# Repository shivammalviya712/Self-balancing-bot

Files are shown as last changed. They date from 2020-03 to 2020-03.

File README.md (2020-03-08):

# Objective

The objective is to make a remote control robot capable of balancing itself using Linear Quadratic Regulator (LQR) Control.

# Components
- Arduino Mega
- MPU 6050 (Accelerometer + Gyroscope)
- DC Motors with quadrature encoders
- Xbee Module 
- Motor Driver (L298N)
- 12V Lipo Battery
- Chassis
- Breadboard
- Wheels

# 3D Model of Chassis
- 3D Modelling of the robot is done in the solidworks, and those files are available in 3D Model folder.
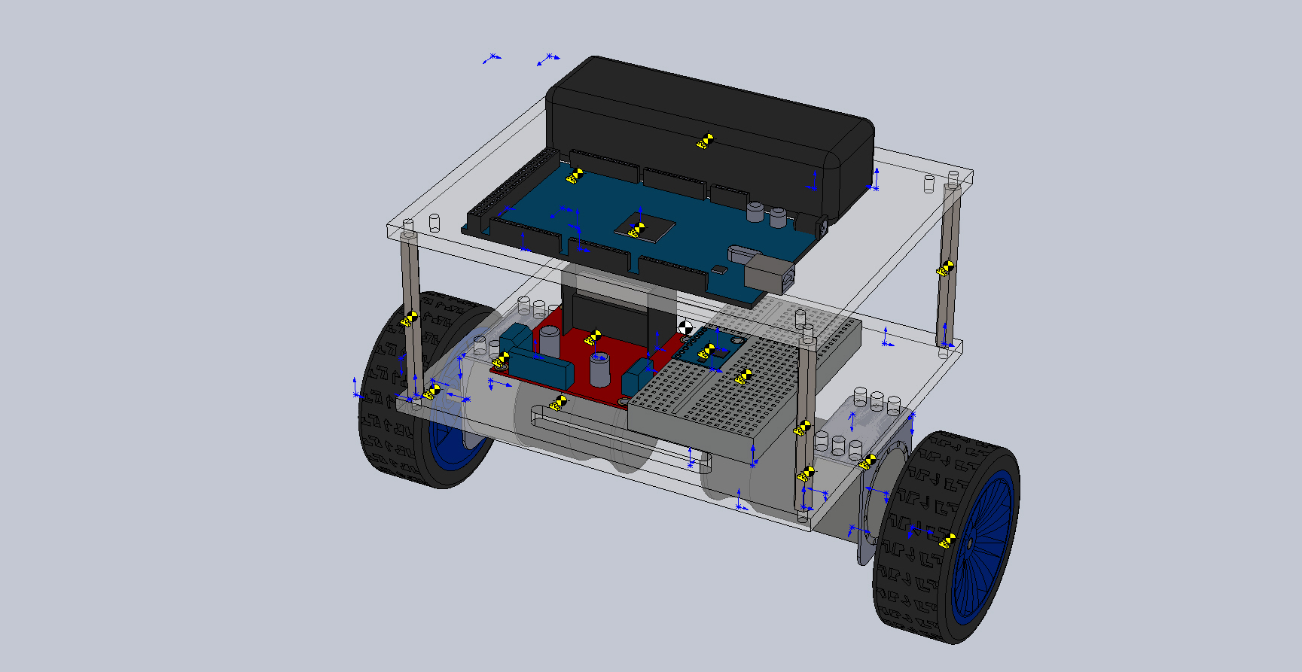
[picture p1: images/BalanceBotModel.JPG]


# Mathematical Model
- Derivations are given in the folder Mathematical Model.
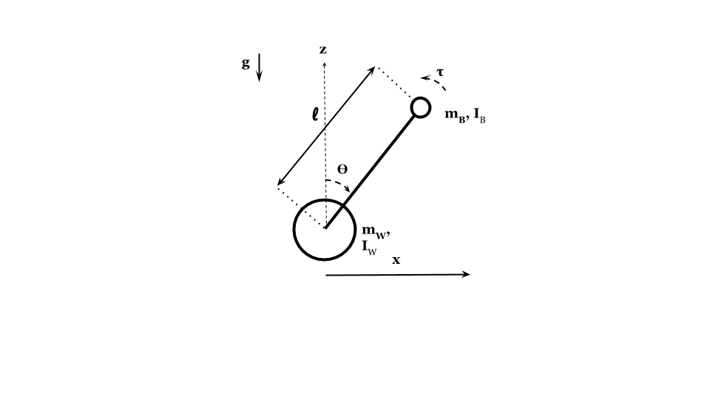
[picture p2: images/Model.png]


- State-Space Equation
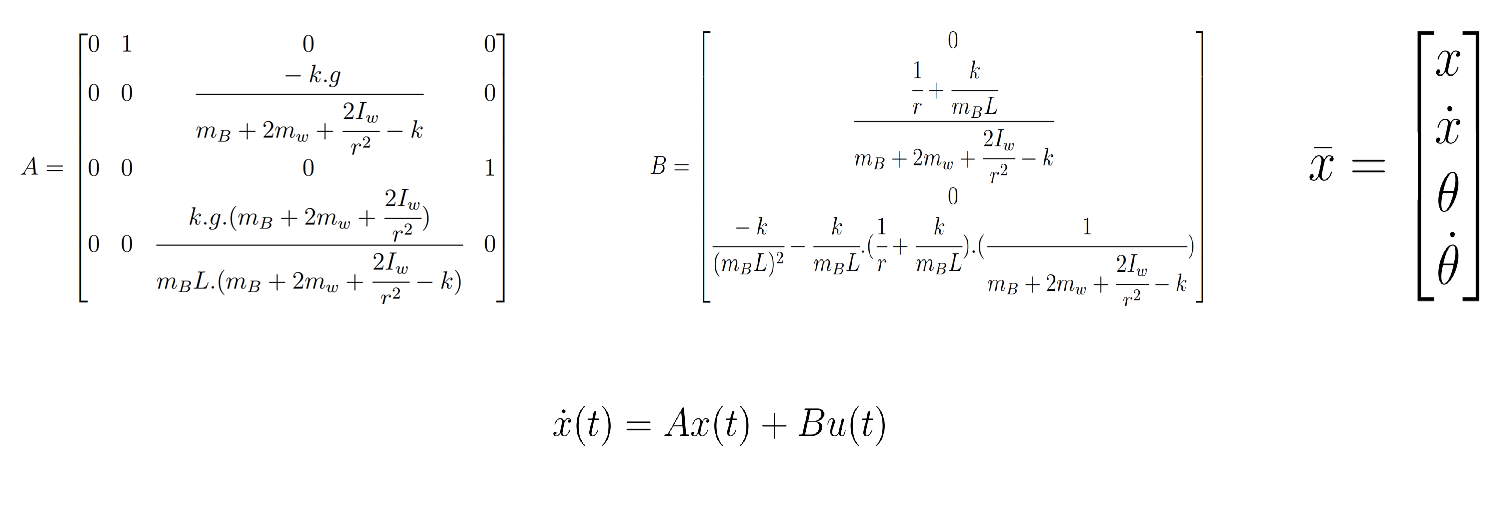
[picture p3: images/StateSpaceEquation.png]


# Control Architecture
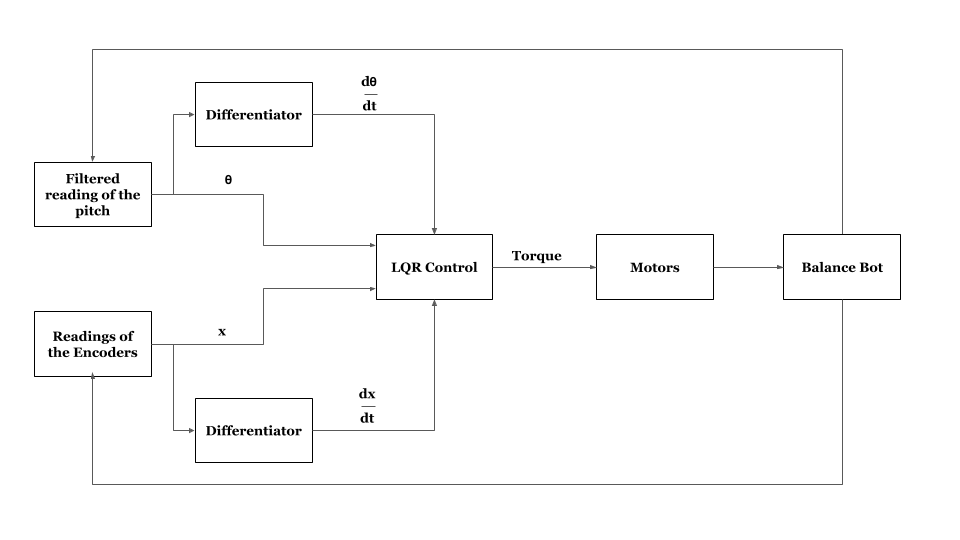
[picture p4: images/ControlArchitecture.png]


- Filter
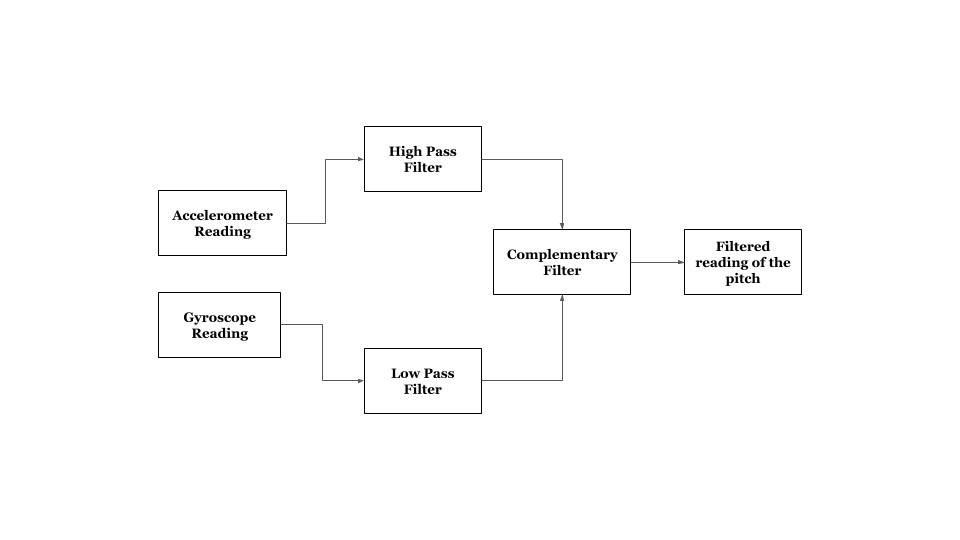
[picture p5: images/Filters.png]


# Code Structure

## main.ino
- This is the file in which code for controlling Arduino Mega is written.

## Encoders
- In these files, class of encoders is defined.  
- X4 encoding is used.

## Motor
- In these files, class of motor is defined.
- Encoder is a inner class of motor.

## TimerInterruptsLib
- Timers 3, 4, and 5 are initialized in this library.

## RCModule
- In this files, class of Xbee is defined.

## Octave
- In this files, dicrete state-space model of robot is calculated from its continuous state-space model.
- State variables are simulated from given Q and R matrix.

# Requirements
- Arduino IDE
  - digitalWriteFast.h
  - MPU6050
  - MPULib
  - I2C
  - I2Cdev
  
- Octave
  - "control" package

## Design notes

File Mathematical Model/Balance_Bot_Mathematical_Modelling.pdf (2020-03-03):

# Mathematical Modelling

mB = Mass of the body
mw = Mass of the wheel
IB = Moment of inertia of the body about the axis of wheels
Iw = Moment of inertia of the wheel
L = Height of the centre of mass of the body from the centre of the wheels r = Radius of the wheels
T = Torque due to both the wheels

φ = The angular velocity of the wheel about its axis of rotation. x = Position of centre of mass of wheel along x-axis
x˙ = Linear velocity of centre of mass of the wheel
θ = Angle between z-axis and body of the robot
˙θ = Angular velocity of the body

Ek = Kinetic Energy
Ep = Potential Energy with the plane through centre of mass of wheels as reference

Assuming the motion of wheels to be pure rolling
x = rφ

φ˙ =

x˙
r

Derivation

Ek = (mw +

mB
2

+

Iw
r

2

)( ˙x)

2 +

(mBL

2 + IB)

2

(

˙θ)

2 + mBL ˙θx˙ cos(θ)

Ep = mBgL cos(θ)

L = Ek − Ep = (mw +

mB
2

+

Iw
r

2

)( ˙x)

2 +

(mBL

2 + IB)

2

(

˙θ)

2 + mBL ˙θx˙ cos(θ) − mBgL cos(θ)

∂L
∂θ = mBL sin(θ)(g − ˙θx˙)

d
dt(

∂L
∂

˙θ

) = (mBL

2 + IB)

¨θ + mBLx¨ cos(θ) − mBLx˙

˙θ sin(θ)

∂L
∂x = 0

d
dt(

∂L
∂

˙θ

) = (mB + 2mw + 2

Iw
r

2

)¨x + mBL¨θ cos(θ) − mBL ˙θ
2
sin(θ)

1

By Euler-Lagrange Equation Q = Generalised Force
q = Generalised Co-ordinates d
dt(

∂L
∂q˙

) −

∂L
∂q = Q

Equations of Motion

¨θ =

mBgL sin(θ) − mBLx¨ cos(θ) − T (mBL² + IB)

(mB + 2mw + 2

Iw
r

2

)¨x + mBL¨θ cos(θ) − mBL ˙θ
2
sin(θ) =

T
r

For sake of simplicity let’s take k =

m²
BL

2
mBL² + IB
From Equations of Motion

x¨ =

1

mB + 2mw +

2Iw
r

2

− kcos(θ)

2

.(−k.g.cos(θ).sin(θ) + mBL

2 ˙θ
2
sin(θ) + (

1
r

+

k.cos(θ)
mBL

).T)

x¯ =

x
x˙
θ
˙θ

By solving x¯˙ = f(¯x) = 0 the equilibrium point we get are :

x
0
0
0

(Unstable),

x
0
π
0

(Stable)

Here x (first element of x¯) is free to take any value.

Let’s x¯o =

x
0
0
0

(Unstable Equilibrium)

Linearising x¯˙ = f(¯x) about x¯o ∂x¨
∂x(at x¯o) = 0

∂x¨
∂x˙

(at x¯o) =

1

mB + 2mw +

2Iw
r

2

− k

.0 = 0

2

∂
x¨
∂θ

(at

x¯o) =

1

m

B + 2

m
w

+

2

### Iwr²

−

k.(

−k.g

)

∂
x¨
∂ ˙θ

(at

x¯o) =

1

m

B + 2

m
w

+

2

### Iwr²

−

k.0 = 0

∂
x¨
∂T

(at

x¯o) =

1r
+

k
m
B

L

m

B + 2

m
w

+

2

### Iwr²

−
k

¨θ
=

k.g.sin

(
θ

)
m
B

L

−

k.x.cos ¨

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
x¯o) = 0

∂

¨θ

∂

x˙(at

x¯o) = 0

∂

¨θ

∂θ

(at

x¯o) =

k.g mBL. m

B + 2

m
w

+

2

### Iwr²

m

B + 2

m
w

+

2

### Iwr²

−
k

∂

¨θ

∂ ˙θ

(at

x¯o) = 0

∂

¨θ

∂T

(at

x¯o) =

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
). | 1 mB + 2mw

+

2

### Iwr²

−
k

A
=
0 1 | 0 | 0
0 0 | − k.g

m

B + 2

m
| w

+

2

### Iwr²

−
k
| | 0
0 0 | 0 | 1

0 0

k.g.

(
m
| B + 2

m
w

+

2

### Iwr²

)

m

BL.

(
m
| B + 2 m
w

+

2

### Iwr²

−
k

)

| | 0

3

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

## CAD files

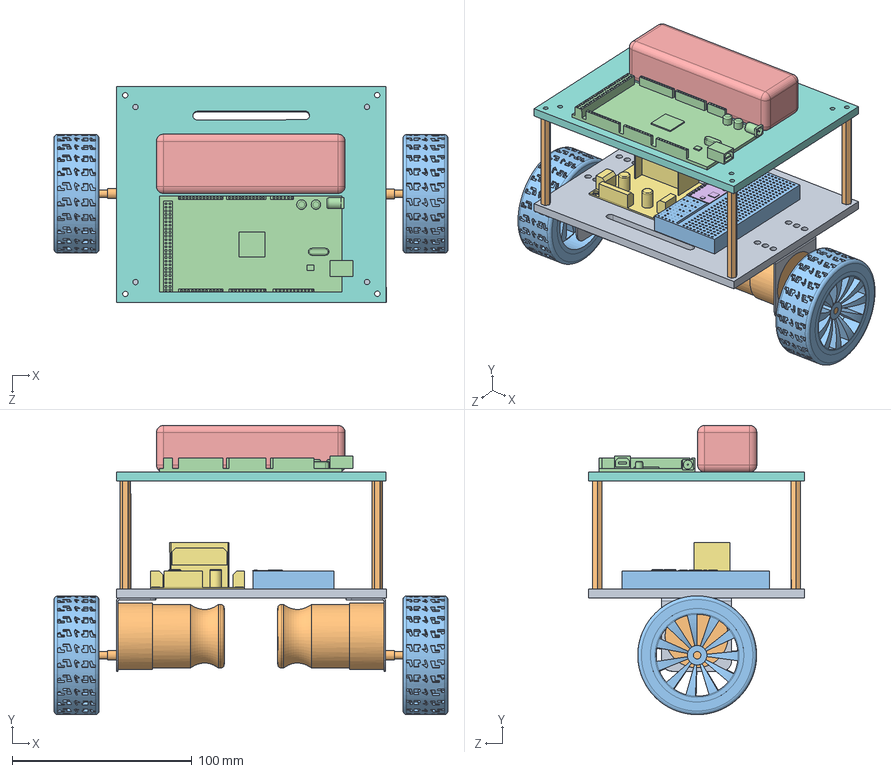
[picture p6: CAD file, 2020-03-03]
3D Model/Balance Bot/Bot.SLDASM
219.1 x 160.8 x 120.1 mm
Motor clamp x 2
Motor x 2
Wheel x 2
Arduino Mega
Battery
GY87
Motor driver
MidPlate
BottomPlate
Rod(6) x 4
Breadboard

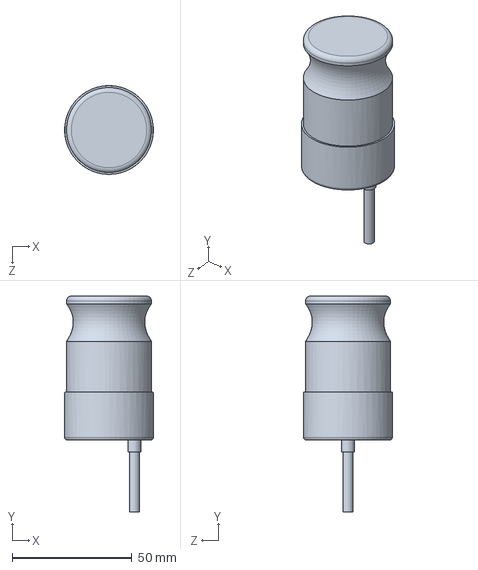
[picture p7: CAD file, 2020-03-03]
3D Model/Balance Bot/Motor.SLDPRT
37.0 x 90.0 x 37.0 mm

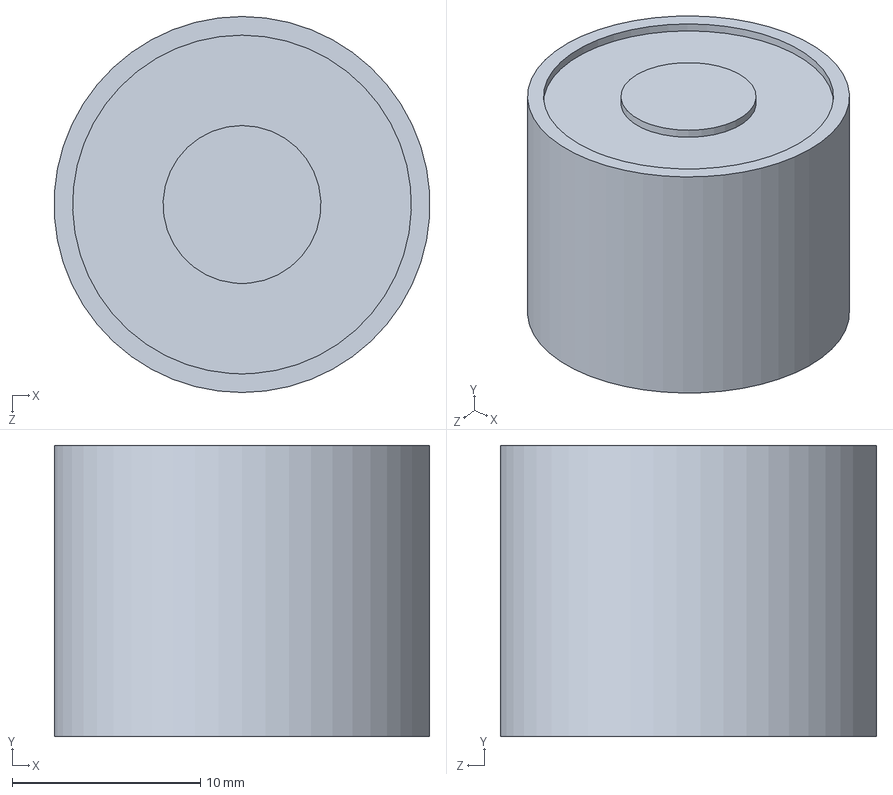
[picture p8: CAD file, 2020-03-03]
3D Model/Balance Bot/Electromagnet.SLDPRT
20.0 x 15.5 x 20.0 mm

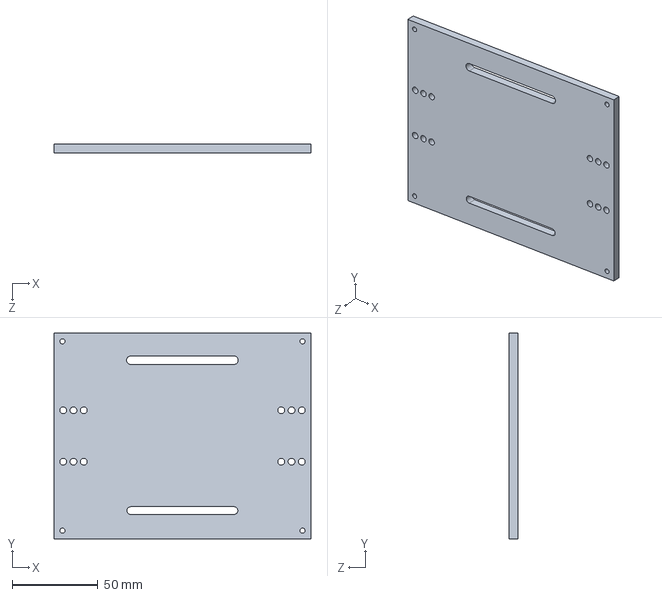
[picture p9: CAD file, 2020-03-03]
3D Model/Balance Bot/BottomPlate.SLDPRT
150.0 x 120.0 x 5.00 mm

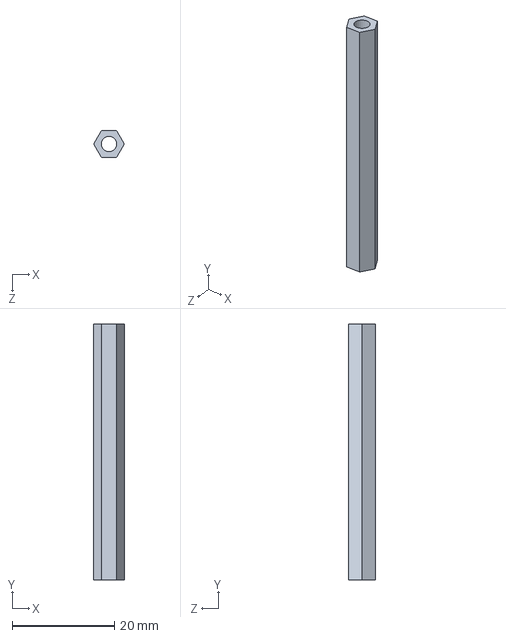
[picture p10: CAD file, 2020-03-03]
3D Model/Balance Bot/Rod(5).SLDPRT
6.00 x 50.0 x 5.20 mm

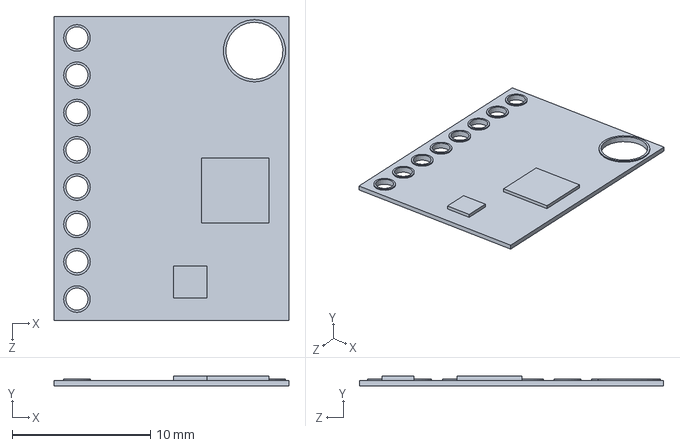
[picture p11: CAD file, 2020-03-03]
3D Model/Balance Bot/GY87.SLDPRT
17.0 x 0.7 x 22.0 mm

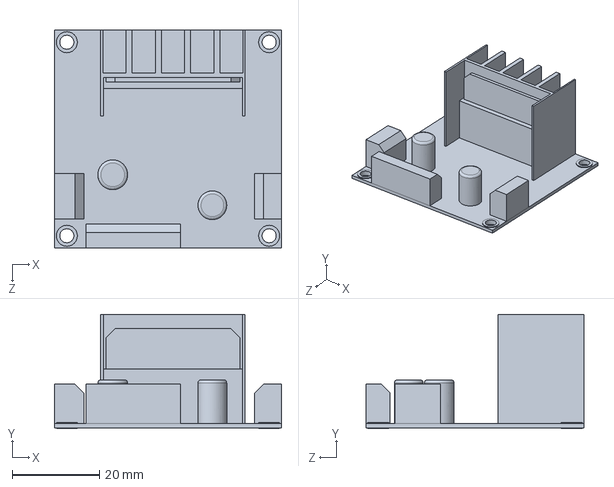
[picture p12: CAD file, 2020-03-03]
3D Model/Balance Bot/Motor driver.SLDPRT
52.0 x 26.2 x 50.0 mm

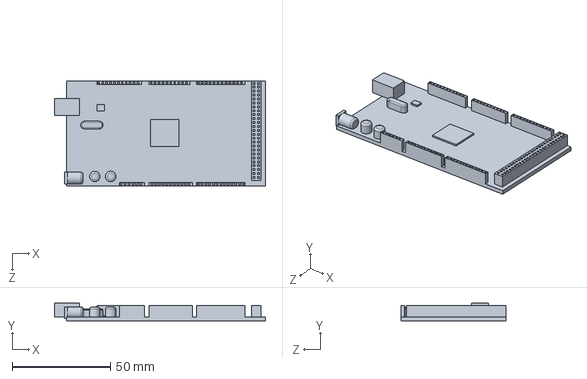
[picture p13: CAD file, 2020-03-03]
3D Model/Balance Bot/Arduino Mega.SLDPRT
107.5 x 9.00 x 53.3 mm

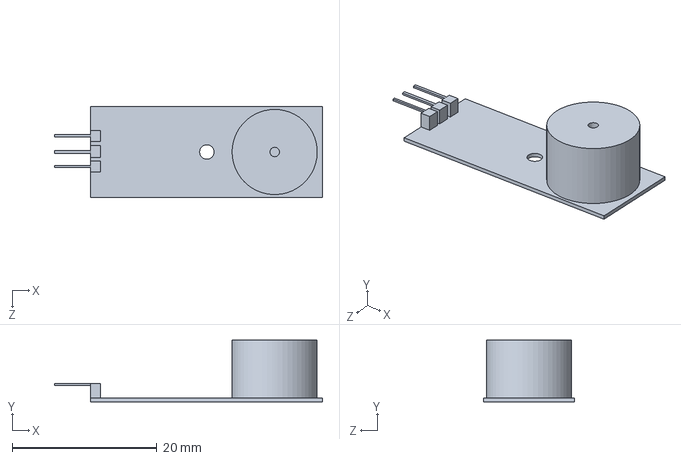
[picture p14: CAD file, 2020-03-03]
3D Model/Balance Bot/Buzzer.SLDPRT
37.0 x 8.50 x 12.5 mm

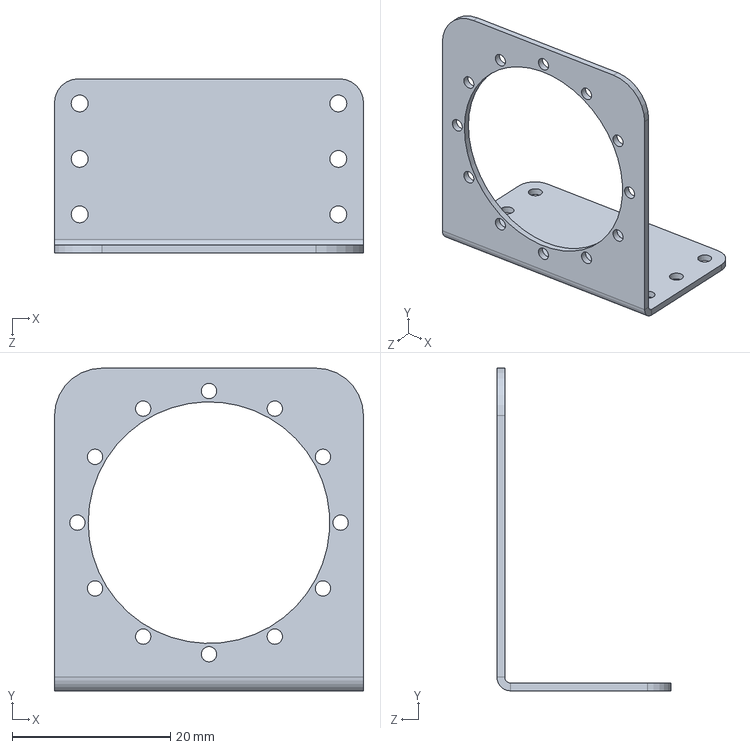
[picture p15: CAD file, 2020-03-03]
3D Model/Balance Bot/Motor clamp.SLDPRT
39.0 x 40.7 x 22.0 mm

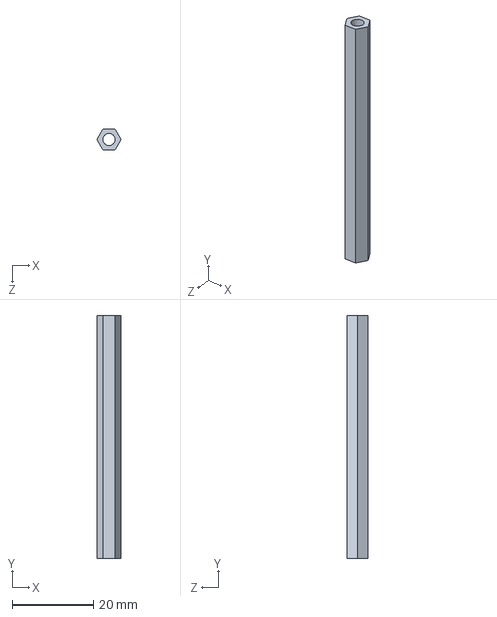
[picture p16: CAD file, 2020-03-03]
3D Model/Balance Bot/Rod(6).SLDPRT
6.00 x 60.0 x 5.20 mm

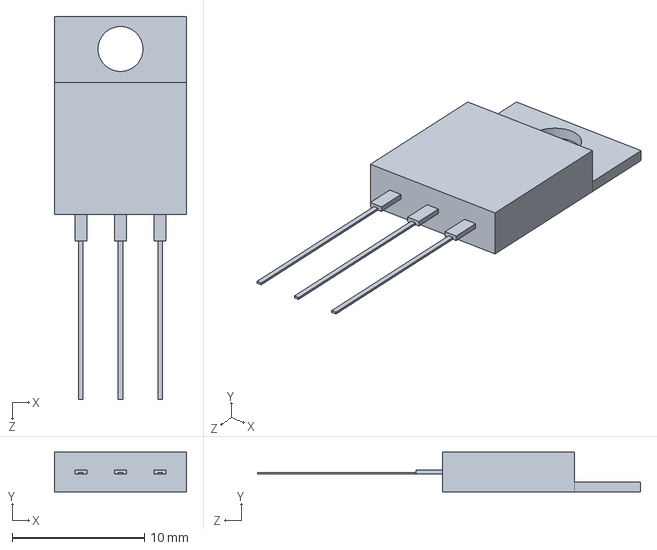
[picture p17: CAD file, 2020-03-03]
3D Model/Balance Bot/IRF540N.SLDPRT
10.0 x 3.00 x 29.0 mm

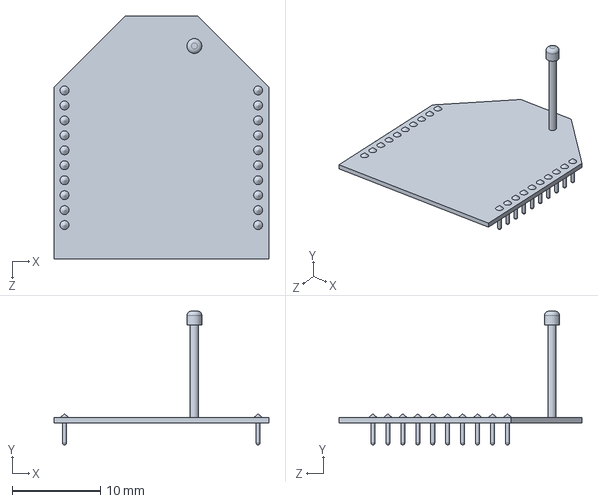
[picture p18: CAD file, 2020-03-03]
3D Model/Balance Bot/Xbee.SLDPRT
24.4 x 15.2 x 27.6 mm

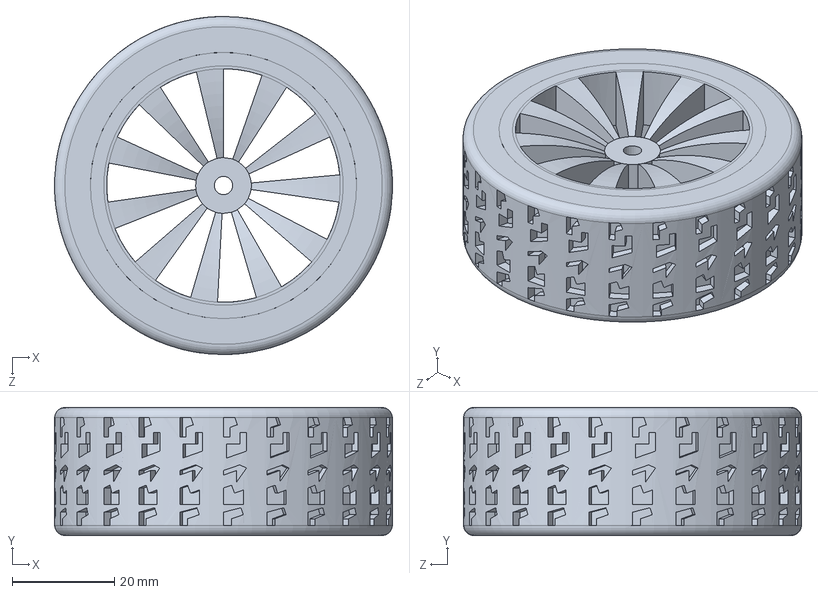
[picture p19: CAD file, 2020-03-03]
3D Model/Balance Bot/Wheel.SLDPRT
66.0 x 25.0 x 66.0 mm

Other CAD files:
3D Model/Balance Bot/TopPlate.SLDPRT
3D Model/Balance Bot/MidPlate.SLDPRT
3D Model/Balance Bot/LED.SLDPRT
3D Model/Balance Bot/Breadboard.SLDPRT
3D Model/Balance Bot/Battery.SLDPRT

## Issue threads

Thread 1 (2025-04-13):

Mistake in the pdf attached for the mathematical model

WizardChrome3700, 2025-04-13:
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

Here in page two of the mathematical model pdf, x_doubledot had L^2 with theta_dot^2.

But in Simulation.m file of Simulation folder.

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

theta_dot^2 is multiplied with L. Also the formula in Mathematical model pdf doesn't pass dimensionality test.

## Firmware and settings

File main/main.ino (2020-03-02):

#include "I2Cdev.h"
#include "i2c_lib.h"
#include "TimerInterrupts.h"
#include "MPU6050.h"
#include <Motor.h>

#define ACCEL_YOUT_H 0x3D  
#define ACCEL_ZOUT_H 0x3F 
#define GYRO_XOUT_H 0x43

const int MPUAddress = 0x68 << 1; // Device address in which is also included the 8th bit for selecting the mode, read in this case.

double K[] = {0, 0, 0, 0}; 
int Kval;
double d0=,md0=,d1=,md1=,d2=,md2=,d3=,md3=;

int16_t ay, az, gx;
uint8_t tmpBytesArr2[2];

const byte lM1 = 22;  //M1 - OUT1 - IN1 - 22
const byte lM2 = 23;  //M2 - OUT2 - IN2 - 23
const byte lME = 11;  //ENA - 11
const byte lMA = 18;  //A - 18
const byte lMB = 17;  //B - 17

const byte rM1 = 30;  //M2 - OUT4 - IN4 - 30
const byte rM2 = 31;  //M1 - OUT3 - IN3 - 31
const byte rME = 12;  //ENB - 12
const byte rMA = 19;   //A - 19
const byte rMB = 16;   //B - 16

const double fCut = 5.0;
const double alpha   = 0.05;
const double dT = 2e-3;
const double Tau = 1/(2*PI*fCut);
const double alphaHPF = Tau/(Tau+dT);
const double alphaLPF = Tau/(Tau+dT);

volatile double accFy, accFz, gyFx, gxVal, gxPrev;
volatile double pitch, pitchPrev, pitchRate; 
volatile unsigned long timeStampTimer5, currTimeTimer5, dT5;


MPU6050 mpu;
Motor leftMotor(lM1, lM2, lME, lMA, lMB, 200);
Motor rightMotor(rM1, rM2, rME, rMA, rMB, 200);

void setup() {
  Serial.begin(115200);
  initMPUSensor();
  attachMotorInterrupts();
  initTimer3();
  initTimer4();
  initTimer5();
  sei();
  
}

void loop() {
  delay(5);
//  Serial.print("X: ");
//  Serial.println(x());
//  Serial.print("XDot: ");
//  Serial.println(xDot());
//  Serial.print("Pitch: ");
//  Serial.println(pitch);  
//  Serial.print("PitchRate: ");
//  Serial.println(pitchRate);
//  leftMotor.forward(200);
//  rightMotor.forward(200);
if (Serial.available() > 0) {
    Kval = Serial.read();
    switch(Kval)
    {
      case 49:
      K[0] = K[0] + d0;
      break;

      case 50:
      K[0] = K[0] + md0;
      break;

      case 51:
      K[1] = K[1] + d1;
      break;

      case 52:
      K[1] = K[1] + md1;
      break;

      case 53:
      K[2] = K[2] + d2;
      break;

      case 54:
      K[2] = K[2] + md2;
      break;

      case 55:
      K[3] = K[3] + d3;
      break;

      case 56:
      K[3] = K[3] + md3;
      break;
    }
    while(Serial.available()) Serial.read();
  }
}

ISR(TIMER3_COMPA_vect) {
    leftMotor.encoder.phiDot = 0.01163552835 * (leftMotor.encoder.rotation - leftMotor.encoder.lastRotation) / SAMPLING_TIME; //0.01163552835 = 2 * M_P! / 540.0
    rightMotor.encoder.phiDot = 0.01163552835 * (rightMotor.encoder.rotation - rightMotor.encoder.lastRotation) / SAMPLING_TIME; //0.01163552835 = 2 * M_P! / 540.0
    leftMotor.encoder.lastRotation = leftMotor.encoder.rotation;
    rightMotor.encoder.lastRotation = rightMotor.encoder.rotation;        
}

ISR(TIMER5_COMPA_vect){
  double torque, voltage; 
  torque = -(K[0]*x() + K[1]*xDot() + K[2]*pitch*PI/180 + K[3]*pitchRate*PI/180);
  voltage = (RESISTANCE*torque/(MOTOR_CONSTANT*GEAR_RATIO)); //+ (xDot()/0.03)*GEAR_RATIO*MOTOR_CONSTANT;
  driveMotors(voltage);  
}

ISR(TIMER4_COMPA_vect){
  check_status(i2c_read_multi_byte(MPUAddress, ACCEL_YOUT_H, 2, tmpBytesArr2));
  ay = ((int16_t)tmpBytesArr2[0] << 8) | tmpBytesArr2[1];
  check_status(i2c_read_multi_byte(MPUAddress, ACCEL_ZOUT_H, 2, tmpBytesArr2));
  az = ((int16_t)tmpBytesArr2[0] << 8) | tmpBytesArr2[1];
  check_status(i2c_read_multi_byte(MPUAddress, GYRO_XOUT_H, 2, tmpBytesArr2));
  gx = ((int16_t)tmpBytesArr2[0] << 8) | tmpBytesArr2[1];

  gxVal = (double)gx/131.0;
  
  accFy = alphaLPF*accFy+(1-alphaLPF)*ay;
  accFz = alphaLPF*accFz+(1-alphaLPF)*az;
  gyFx = (1-alphaHPF)*(gxVal-gxPrev)+(1-alphaHPF)*gyFx;

  pitchPrev = pitch;
  pitch = (1-alpha)*(dT*gyFx+pitch)-alpha*atan2(accFy, abs(accFz))*180/PI;
  pitchRate = (pitch-pitchPrev)/dT;
}

double x() {
  return leftMotor.encoder.getX();
}

double xDot() {
  return leftMotor.encoder.getXDot();
}

void check_status(STAT status){
  if(status != OK){
    Serial.print("ERROR: ");
    Serial.println(status);
  }
}

void initMPUSensor(void){
  
  Wire.begin();

  // initialize device
  Serial.println("Initializing I2C devices...");
  mpu.initialize();
  
  // verify connection
  Serial.println("Testing device connections...");
  Serial.println(mpu.testConnection() ? "MPU6050 connection successful" : "MPU6050 connection failed");

  Serial.println("Updating internal sensor offsets...");

  mpu.setXGyroOffset(13);
  mpu.setYGyroOffset(47);
  mpu.setZGyroOffset(-916);

  mpu.setXAccelOffset(-3768);
  mpu.setYAccelOffset(-1314);
  mpu.setZAccelOffset(1419);

  Serial.print(mpu.getXAccelOffset());Serial.print("\t");
  Serial.print(mpu.getYAccelOffset());Serial.print("\t");
  Serial.print(mpu.getZAccelOffset());Serial.print("\t");
  Serial.print(mpu.getXGyroOffset());Serial.print("\t");
  Serial.print(mpu.getYGyroOffset());Serial.print("\t");
  Serial.print(mpu.getZGyroOffset());Serial.print("\t");Serial.print("\n");
  
  i2c_init();
  Serial.println("I2C Reset");
  Serial.println(TWSR, HEX);
  pitch = accFy = accFz = gxPrev = gyFx = 0;
}

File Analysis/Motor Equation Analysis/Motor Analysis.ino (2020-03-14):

#include <TimerInterrupts.h>
#include <Motor.h>

const byte lM1 = 22;  //M1 - OUT1 - IN1 - 22
const byte lM2 = 23;  //M2 - OUT2 - IN2 - 23
const byte lME = 11;  //ENA - 11
const byte lMA = 18;  //A - 18
const byte lMB = 17;  //B - 17

const byte rM1 = 30;  //M1 - OUT4 - IN4 - 30
const byte rM2 = 31;  //M2 - OUT3 - IN3 - 31
const byte rME = 12;  //ENB - 12
const byte rMA = 19;   //A - 19
const byte rMB = 16;   //B - 16

double torque, voltage;
unsigned long deltaT = 0;

Motor leftMotor(lM1, lM2, lME, lMA, lMB);
Motor rightMotor(rM1, rM2, rME, rMA, rMB);

void setup() {
  Serial.begin(115200);
  attachMotorInterrupts();
//  initTimer3();
  sei();  
}

void loop() {
  Serial.println();
  int analogVol;
  for (voltage = 0; voltage <= 12; voltage += 0.01)
  {
    analogVol = (int) (voltage*255.0/12.0 + 0.5);
    leftMotor.generate(analogVol);
    Serial.print("Voltage = ");
    Serial.println(voltage);
    Serial.print("Omega = ");
    Serial.println(leftMotor.encoder.phiDot);
    delay(100);
  }
  Serial.println();
}

//ISR(TIMER3_COMPA_vect) {
//    leftMotor.encoder.phiDot = (0.02243994753 / ENCODING) * (leftMotor.encoder.rotation - leftMotor.encoder.lastRotation) / SAMPLING_TIME; //0.02243994753 = 2 * M_P1 / 280.0
//    rightMotor.encoder.phiDot = (0.02243994753 / ENCODING) * (rightMotor.encoder.rotation - rightMotor.encoder.lastRotation) / SAMPLING_TIME; //0.02243994753 = 2 * M_P1 / 280.0
//    leftMotor.encoder.lastRotation = leftMotor.encoder.rotation;
//    rightMotor.encoder.lastRotation = rightMotor.encoder.rotation;        
//}

double x() {
  return leftMotor.encoder.getX();
}

double xDot() {
  return leftMotor.encoder.getXDot();
}

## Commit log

2020-03-14 Analysis of Data from Motor
    [Motor Equation.xlsx]
2020-03-14 Analysis libraries and code.
    [Motor Data Analysis.xlsx]
2020-03-15 Motor Equation Analysis Update
    [Motor Data Analysis.xlsx, motorDataAnalysis.xlsx]
